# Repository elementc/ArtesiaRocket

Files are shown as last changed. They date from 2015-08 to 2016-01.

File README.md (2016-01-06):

# ArtesiaRocket
Repository of (eventually) open-source model rocket components. Shares a name with an area of Port Canaveral [before it was Port Canaveral](http://www.cityofcapecanaveral.org/index.asp?Type=B_BASIC&SEC=%7BFCF82651-D0DA-4BE5-B512-1652A96826AE%7D).

# Current Build
We emulate an existing simple Estes rocket (the EX-200) which features a mini engine mount. While all the structural components are printable,  there will always be some [vitamins](http://reprap.org/wiki/Category:Vitamin) in need of collection.

## Bill of Materials
* 1 x [Estes EX-200 kit](http://www.estesrockets.com/rockets/rtf/002450-ex-200tm), in particular:
  * 1 x Shock cord
  * 1 x Parachute
* 1 x Engine Retention Ring model from physibles/20mm (These are fragile so you may want to print some duplicates. They print fast.)
* 1 x Engine Mount model from physibles/20mm
* 4 x Fin model from physibles/20mm
* 1 x Paraboloid Nose Cone model from physibles/20mm
* 1 x Body Tube 130mm model from physibles/20mm
* 1 x Body Tube 50mm model from physibles/20mm
* 1 x Body Tube Coupler with hook model from physibles/20mm
* Glue (superglue works great!)
* Masking Tape
* Paint

## Assembly
1. Print all physibles. Clean off support materials as needed. Sand until smooth.
2. Glue fins into slots on engine mount. Glue shorter body tube onto engine mount ring.
3. Tie shock cord to coupler inner beam.
4. Glue coupler to other end of shorter body tube.
5. Pull free end of shock cord through long body tube.
6. Glue long body tube to coupler.
7. Tie free end of shock cord to nose cone loop.
8. Apply tape as necessary to nose cone friction mount. Should be able to slide into free body tube end and remain securely but pop off relatively easily.
9. Tie parachute to nose cone loop.
10. Snap engine retention ring into place at bottom of engine mount.
12. Apply paint as desired.

## Printing Pointers
Use calipers to measure your filament diameter. Underextrusion/overextrusion will KILL some of these prints. Print at 100% infill for body tubes, make sure you have good cooling and a SLOW extrusion rate (30mm/s is the our max). For nose cones, smaller infill is better, we use 20%. Complex parts like couplers and nosecones with hooks need support material. Sand all parts to be as smooth as you can get them, especially areas where support material was removed.

# License
Physible designs are generally available under the latest [Creative Commons Attribution-NonCommercial-ShareAlike license](http://creativecommons.org/licenses/by-nc-sa/4.0/).
Source code is under the [Apache License](http://choosealicense.com/licenses/apache-2.0/) unless indicated otherwise in the source.

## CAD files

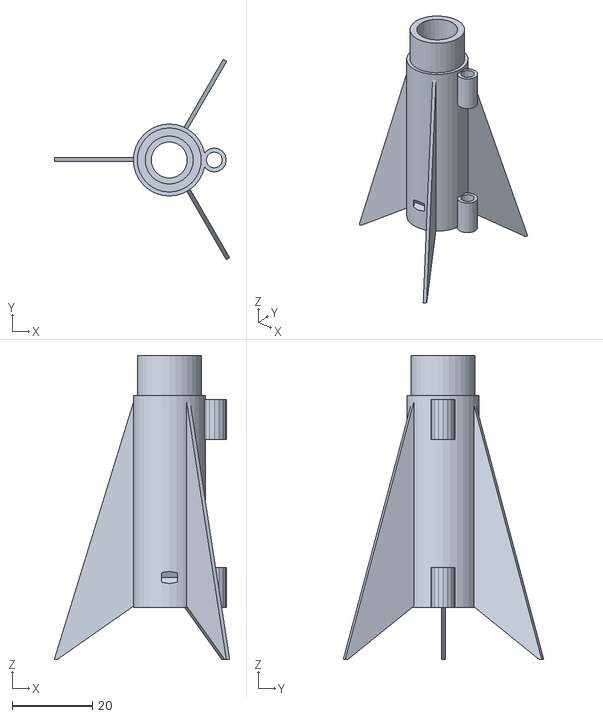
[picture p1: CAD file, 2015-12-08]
physibles/18mm/engine_mount_and_fin_assembly.stl
43.9 x 50.1 x 76.0

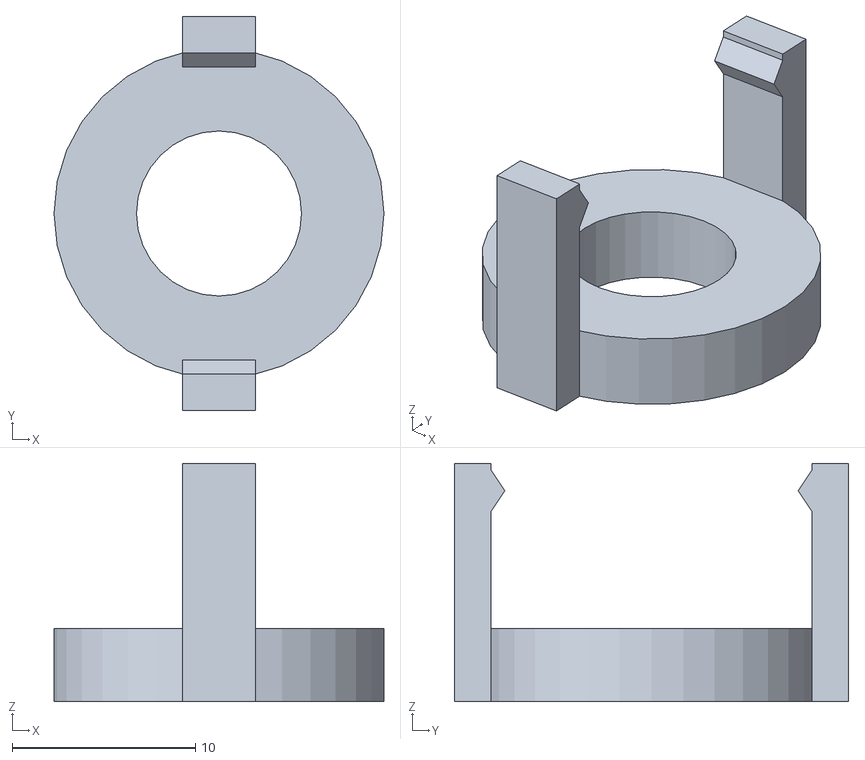
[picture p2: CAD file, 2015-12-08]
physibles/18mm/engine_retention_ring.stl
18.0 x 21.5 x 13.0

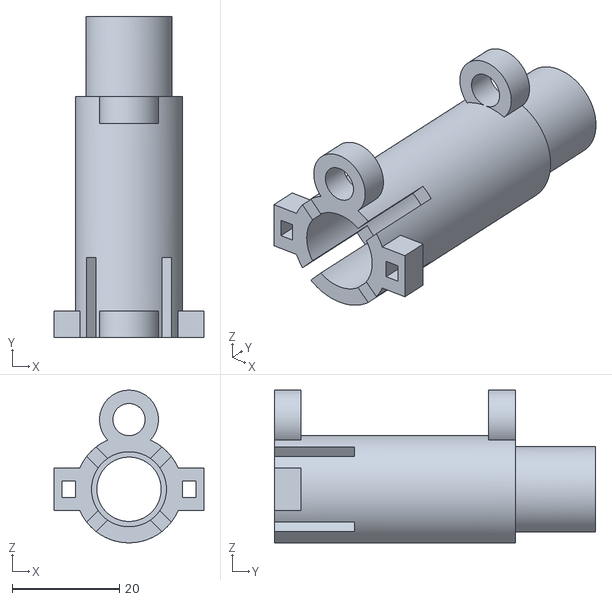
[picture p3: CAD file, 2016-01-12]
physibles/20mm/engine-mount.stl
28.0 x 60.0 x 28.5

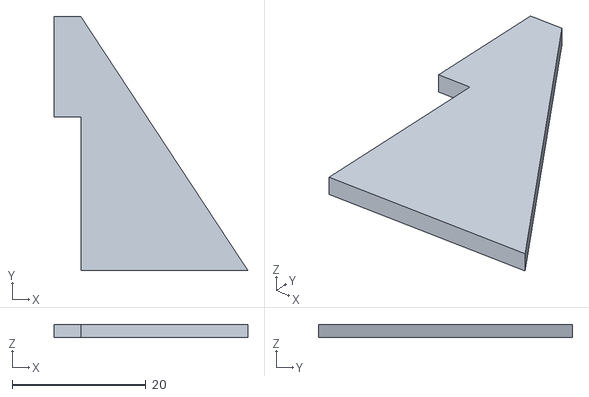
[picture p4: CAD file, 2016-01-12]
physibles/20mm/fin.stl
29.0 x 38.0 x 2.00

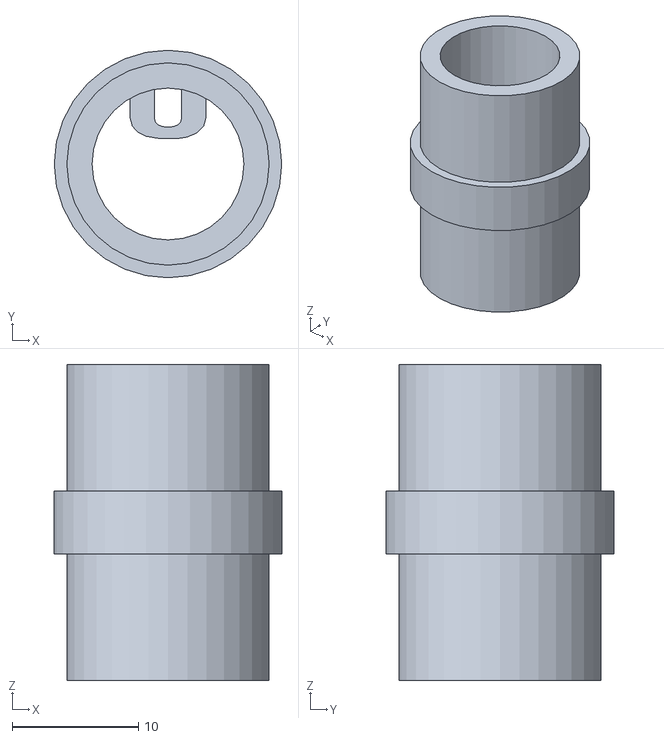
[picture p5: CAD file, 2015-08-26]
physibles/18mm/body_tube_coupler_with_hook.stl
18.0 x 18.0 x 25.0

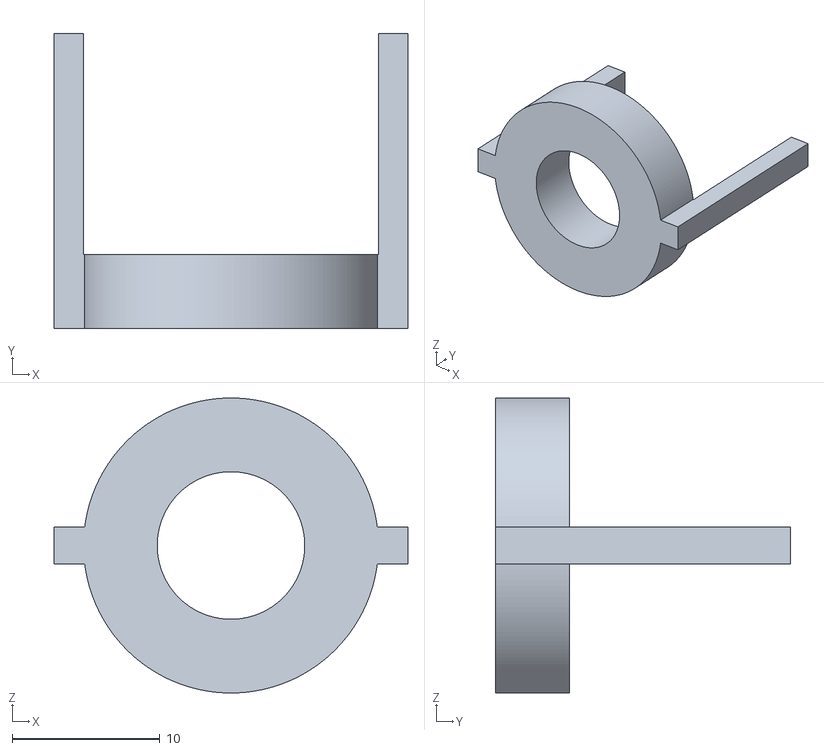
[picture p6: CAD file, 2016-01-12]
physibles/20mm/engine-retention-ring.stl
24.0 x 20.0 x 20.0

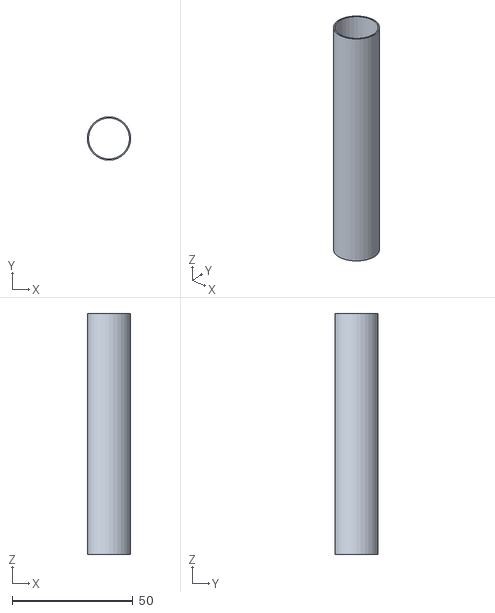
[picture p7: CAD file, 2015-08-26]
physibles/18mm/body_tube_18mmx100mm.stl
18.0 x 18.0 x 100.0

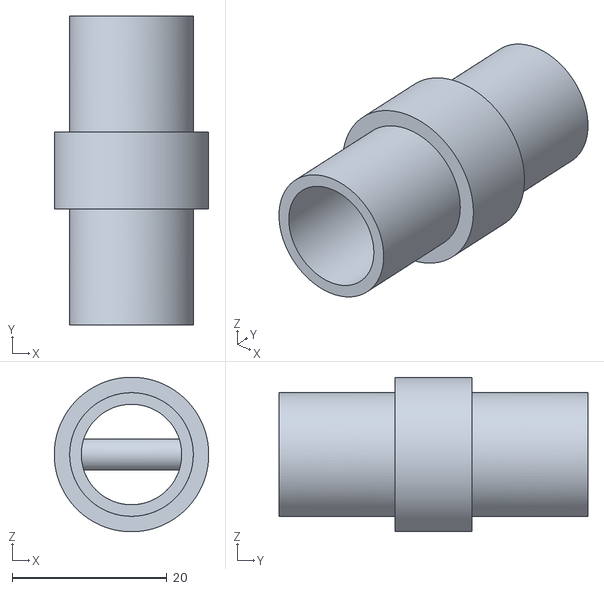
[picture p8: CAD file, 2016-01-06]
physibles/20mm/body-coupler-with-hook.stl
20.0 x 40.0 x 20.0

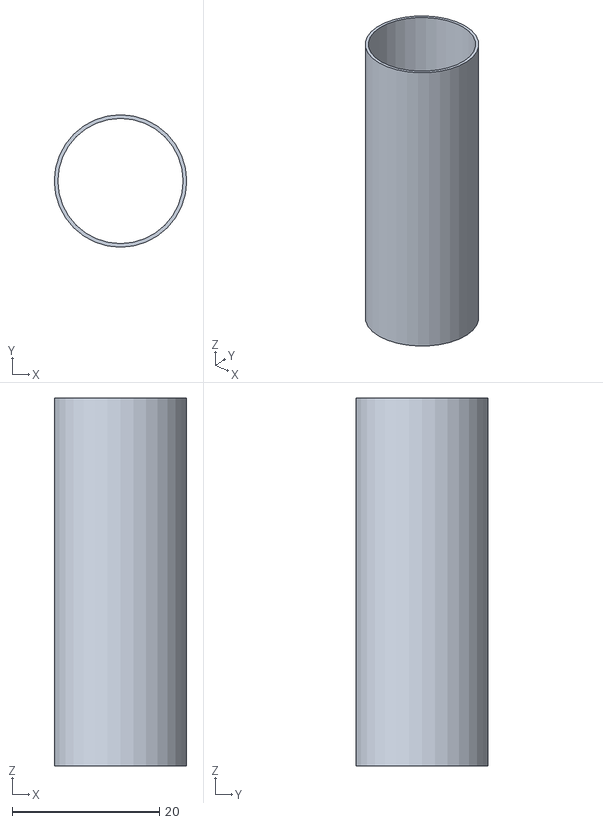
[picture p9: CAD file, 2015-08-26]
physibles/18mm/body_tube_18mmx50mm.stl
18.0 x 18.0 x 50.0

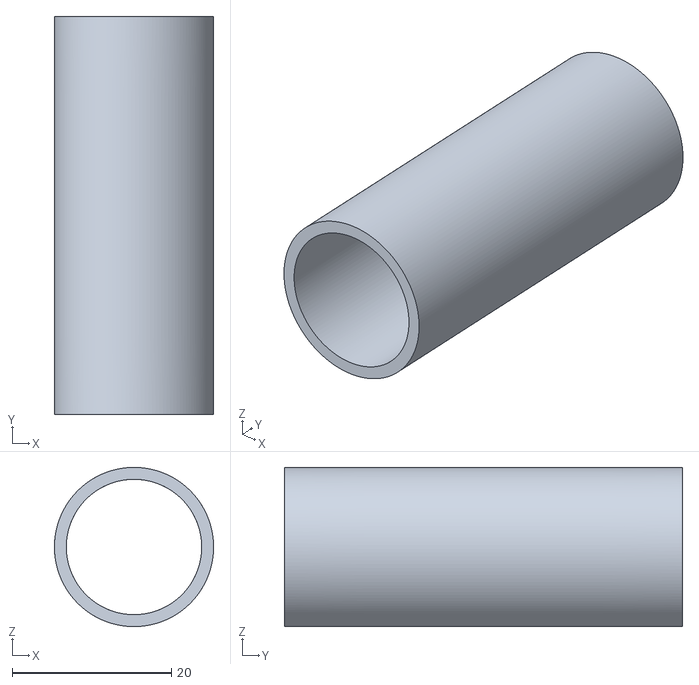
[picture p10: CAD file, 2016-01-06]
physibles/20mm/50mm-body-tube.stl
20.0 x 50.0 x 20.0

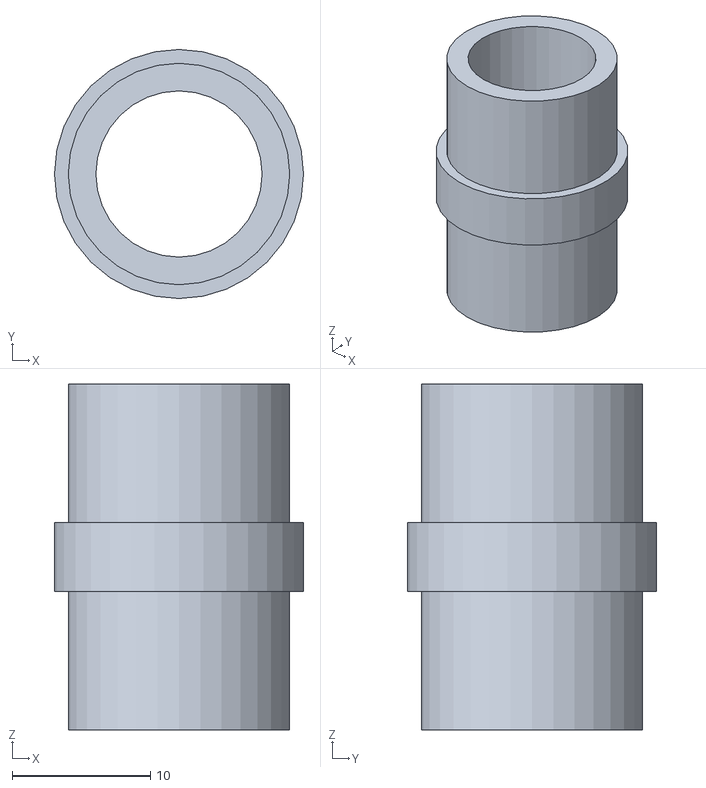
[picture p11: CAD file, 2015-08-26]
physibles/18mm/body_tube_coupler.stl
18.0 x 18.0 x 25.0

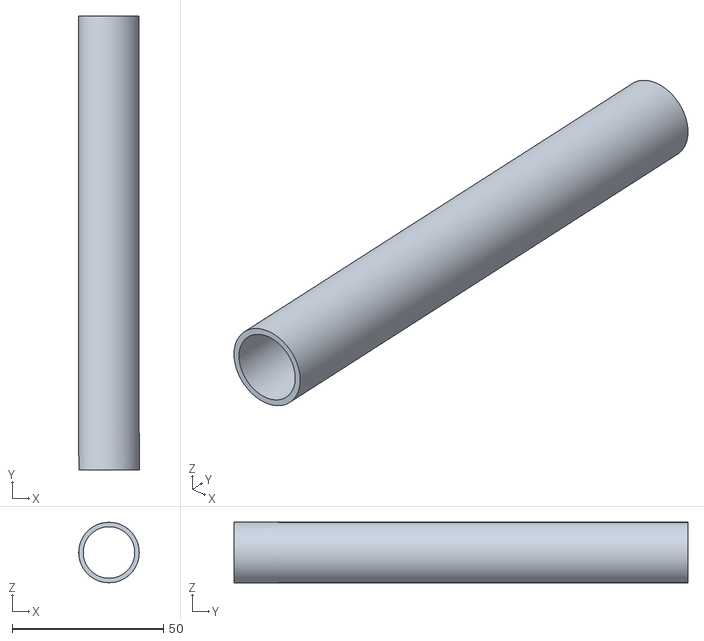
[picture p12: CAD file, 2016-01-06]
physibles/20mm/150mm-body-tube.stl
20.0 x 150.0 x 20.0

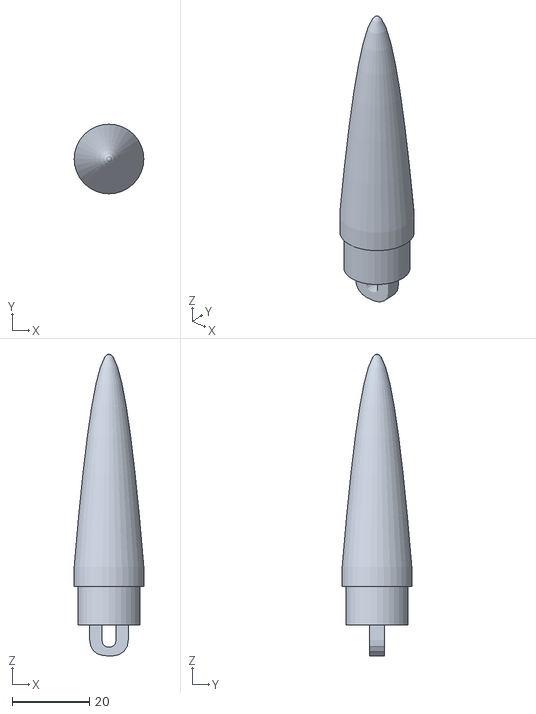
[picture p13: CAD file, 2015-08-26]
physibles/18mm/paraboloid_nose_cone.stl
18.0 x 18.0 x 78.0

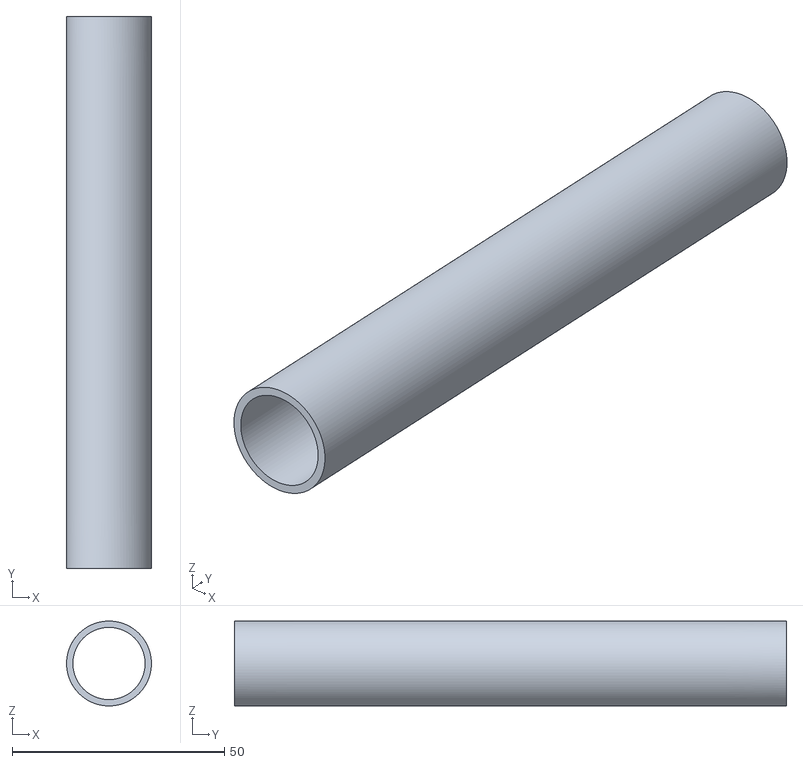
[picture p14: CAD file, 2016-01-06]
physibles/20mm/130mm-body-tube.stl
20.0 x 130.0 x 20.0

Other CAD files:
physibles/18mm/body_tube_18mmx130mm.stl
physibles/20mm/70mm-body-tube.stl
physibles/18mm/body_tube_18mmx75mm.stl
physibles/20mm/body-coupler-no-hook.stl
physibles/20mm/100mm-body-tube.stl
physibles/20mm/parabolic-nose-cone.stl

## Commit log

2015-08-26 add some parts
    [body_tube_18mmx100mm.stl, body_tube_18mmx130mm.stl, body_tube_18mmx50mm.stl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]
2015-12-08 Add engine mount, fin assembly, and retention ring to make entire structure printable.
    [engine_mount_and_fin_assembly.stl, engine_retention_ring.stl]
2016-01-06 add 20mm series
    20mm body parts print much easier on 1mm nozzles. 18mm parts are kept
    for posterity.
    [100mm-body-tube.stl, 130mm-body-tube.stl, 150mm-body-tube.stl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]
2016-01-12 Updated for printability
    [engine-mount.stl, engine-retention-ring.stl, fin.stl]
